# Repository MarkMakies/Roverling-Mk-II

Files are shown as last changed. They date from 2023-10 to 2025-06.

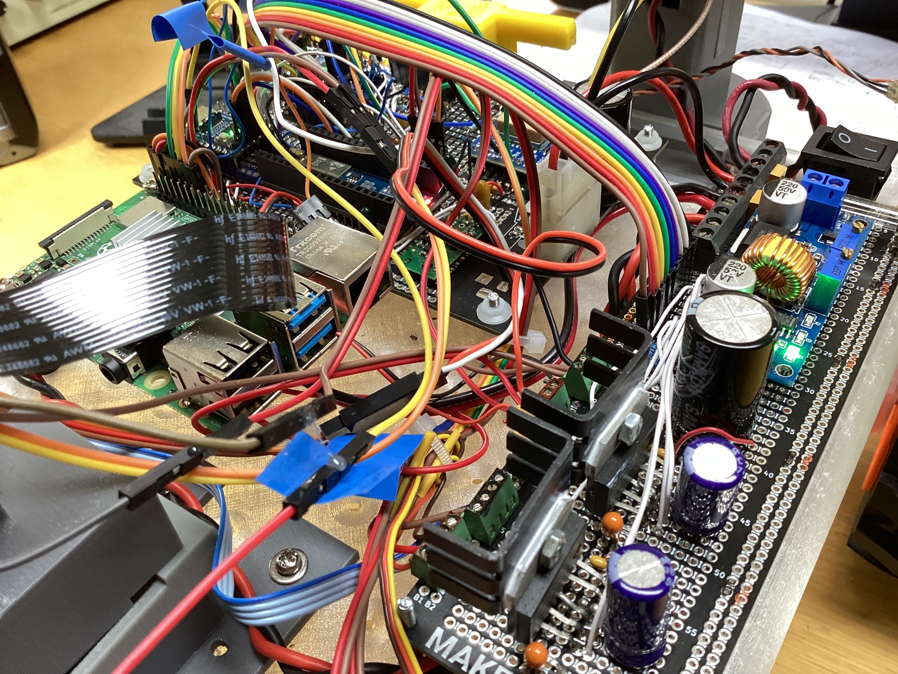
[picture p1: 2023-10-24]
Electronics/IMG_1050.JPEG

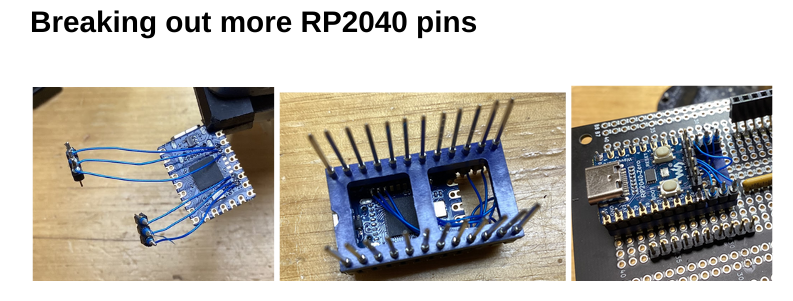
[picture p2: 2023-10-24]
Electronics/Screenshot_2023-10-25_10-17-56.png

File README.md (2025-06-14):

## Roverling Mk II
# A cheap multipurpose mobile robotic platform for research, development, education and fun
All design files, schematics & code available in this repository.  

Build tutorial [here](https://makies.com.au/roverlingmkii/).

**2025 Update:** Started working on an updated version to support my autonomous metal detector project.  Documenting progress on Hackaday.io.  

---

### STAGE 1 - Mecha Design July 2023

cad

### STAGE 1 - Complete Aug 2023

rv2a

### Stage 2 - Tronics design wish list Sep 2023

rv2b

### Stage 2 - MPU code development and electronics complete Oct 2023



### Stage 3 - GUI complete as well as LoRa /WiFi /MQTT gateway.  



## And now, Oct 2023,  writing it all up so others can understand and follow I hope :) 

in progress.....

# Why did I start this project:   

A few months back I created a basic mobile platform using parts from an old 3D printer.  It was fun but not very practical.

I designed Roverling Mark II so I could experiment with a practical, configurable and reliable  mobile platform.  Hopefully one day getting it to do some useful stuff around our bush block, like

      - Searching paddocks for weeds and recording locations.
      - Navigating down a 200m drive to check if the gate is closed.
      - Navigating up the drive 50m to check that the machine shed roller doors are secure.
      - Recording animal sightings on the block.  We’d see up to 50 roos per day on our block.
      - It would be good to identify and scare deer away from our olive grove.
      - And a friend already wants to mount a metal detector and do automatic scanning of a large area.

Anyway, to that end, here is the complete design and everything you need to know to make your own or any variation.  As much as possible I’ve kept the cost down to a minimum, reused some older parts and printed as much as possible.

This is a current work in progress.  At some stage I needed to draw the line and write something up before it gets too big.  So these are the current working and operational specifications

     - 440 mm long x 350 mm wide, 250 mm max height, 200 mm nominal platform height
     - 3.5 kg without battery, uses an 18V power tool battery
     - Up to 22 satellite GNSS receiver, augmentation using SBAS, 1Hz updates
     - IMU: 3x accel, 3x gyro, magnetometer, pressure
     - 2.4Ghz 6 channel RC receiver and decoder, with diverse receiver
     - 2 channel motor quadrature decoders 
     - 2 channel motor current sensors (effectively torque sensors)
     - Sonar, ranger
     - 915 Mhz LoRa module.  Comms at 1800 bps,  64 byte telemetry packet, 16 byte command packet, encrypted, super reliable
      LoRa base station, which is effectively my MQTT gateway for telemetry and commands back
     - Mapping module runs on desktop from MQTT feed to produce realtime tracking info overlaid on an image (for me an old NearMap screenshot).
      On board RPi 4B w/ 4G running the latest OS with a camera 3 module.  

All the 3D design is done in FreeCAD and all the slicing and printing on a Prusa platform.  As well as the actual design files, I’ve also made available stl model files, g-code files and Prusa project files for all parts.

The schematic is done with KiCAD.  I used mixed prototyping methods and no PCB has been designed (yet) so you will need a fair understanding of how to layout and wire correctly.

All the code is in python.  I’ve pretty much written my own drivers for all of the low level stuff except the sx1262 suite for LoRa and MQTT.  I’ve tried to document as much as possible.

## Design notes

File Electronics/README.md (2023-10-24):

## KiCAD schematic diagram in R202 directory.

PCB not yet designed.

First prototype pics give an idea of how to wire.

## Major Parts List

- 1x 	Adafruit Ultimate GPS Breakout with GLONASS + GPS - PA1616D - 99ch 10 Hz
- 1x 	SMA to uFL/u.FL/IPX/IPEX RF Adapter Cable
- 1x 	Makerverse Project Proto - Protoboard with Power Breakouts
- 6x	2.54mm Pitch 4-Pin Screw Terminal Block
- 2x	RP2040-Zero, a Pico-like MCU Board Based on Raspberry Pi RP2040
- 1x	Raspberry Pi Pico W (for LoRa / MQTT gateway)
- 1x	GPS/GNSS Magnetic Mount Antenna SMA - 3m
- 1x	AltIMU-10 v6 Gyro, Accelerometer, Compass, and Altimeter 
- 2x	SX1262 LoRa Node Module for Raspberry Pi Pico, LoRaWAN
- 1x	915MHz LoRa Antenna RP-SMA - 1/4 Wave 2dBi
- 1x	PIR Infrared Motion Sensor (HC-SR501)
- 1x	XL-MaxSonar-EZ0 Sonar Range Finder MB1200
- 1x	DC-DC Adjustable Step-down Module 5A 75W
- 2x	LMD18200, 3A, 55V H-Bridge, or similar

For later projects and video capture only at this stage
- 1x	Raspberry Pi 4 Model B 4GB 
- 1x	Raspberry Pi Camera Module 3

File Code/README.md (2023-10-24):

Which code goes into which MPU...

## Motion Processor
###### (MicroPython v1.20.0 on 2023-04-26; Raspberry Pi Pico with RP2040)

Works independently of other modules.  Can use RC to control without any other modules.
On RC toggle FLAPS to put into RC mode.  Onboard LED will change from steady green to flashing pink.
Ensure throttle is at min first.  Ailerons control steering, elevator controls camera tilt.  GEAR
puts it into reverse mode.

	MPU/mainM.py 			rename to main.py
	MPU/Comms.py                 	inter-MPU Comms
	MPU/QuadDec.py			Motor quadrature decoder (PIO/SM based)
	MPU/RCinterface.py  		6 channel RC interface (interrupt based)

## Telemetry Processor 
###### (MicroPython v1.20.0 on 2023-04-26; Raspberry Pi Pico with RP2040)

Aggregates ALL data from platform for telemetery transmission over LoRa at around 1800bps.  Accepts
LoRa commands. Telemetry includes:

	GPS: 		quality, number satellites, accuracy, altitude, lat & long with 7 decimal places precision
	IMU: 		acceleration (X,Y,Z), gyroscope (X, Y, Z), magnetometer (X, Y, Z), temperature, pressure
	Locomotion: 	velocity (L/R), torque/current (L/R), power delivered (L/R)
	RC: 		6 channels, 0 to 100%
	Platform: 	PIR, sonar range, battery level, status bits
	Comms:  	RSSI & SNR for both Roverling and Base Station ends

&nbsp;
 
	MPU/mainT.py 			rename to main.py
	MPU/GPS.py			Configure and then read GPS module data
	MPU/IMU.py			Intertial measurement unit interface
	MPU/Comms.py			inter-MPU Comms
	MPU/Packets.py			telemetry and control LoRa packet assembly and disassembly
	MPU/Secrets.py			modify and rename Secret_Example.py to Secrets.py
		
	MPU/lib/_sx126x.py 		LoRa drivers from https://github.com/ehong-tl/micropySX126X/tree/master
	MPU/lib/sx1262.py		LoRa drivers from https://github.com/ehong-tl/micropySX126X/tree/master
	MPU/lib/sx126x.py 		LoRa drivers from https://github.com/ehong-tl/micropySX126X/tree/master

## Telemetry Gateway Processor  
###### (MicroPython v1.20.0 on 2023-04-26; Raspberry Pi Pico W with RP2040)

Provides a gateway for Roverling LoRa commands and telemetry to MQTT message broker over WiFi.  Onboard LED
flashes blue when commands are received.  A sigle message is delivered twice a second, and looks a lot like this. (On MQTT Explorer): 
(3172, '-37.0000000, 144.0000000', 1, 4, 3.0, 640.4, 0.0, 0.0, 0.039, 0.043, 0, 0, 10, 50, 51, 51, 9, 10, 0.013, -0.037, 1.015, 0, 0, 0, 0.034, -0.037, 0.455, 19.734, 944.5, 10.25, -42.0, 384, 0, 0, 0, 11.0, -45.0)
	
	MPU/mainG.py 			rename to main.py
	MPU/Packets.py			telemetry and control LoRa packet assembly and disassembly
	MPU/Secrets.py			modify and rename Secret_Example.py to Secrets.py
	
	MPU/lib/_sx126x.py 		LoRa drivers from https://github.com/ehong-tl/micropySX126X/tree/master
	MPU/lib/sx1262.py		LoRa drivers from https://github.com/ehong-tl/micropySX126X/tree/master
	MPU/lib/sx126x.py 		LoRa drivers from https://github.com/ehong-tl/micropySX126X/tree/master
	
	MPU/lib/umqttsimple.py		MQTT module from https://pypi.org/project/micropython-umqtt.simple/#files

## Block Diagram 


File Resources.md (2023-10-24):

### Roverling References

    https://core-electronics.com.au/raspberry-pi-camera-3.html
    https://www.lloydbrombach.com/post/calibrating-a-magnetometer-for-accurate-compass-headings
    https://cdn-shop.adafruit.com/datasheets/GlobalTop-FGPMMOPA6H-Datasheet-V0A.pdf
    https://core-electronics.com.au/raspberry-pi-4-model-b-4gb.html
    https://core-electronics.com.au/dc-dc-adjustable-step-down-module-5a-75w.html
    https://maxbotix.com/pages/xl-maxsonar-ez-datasheet
    https://core-electronics.com.au/modmypi-pir-infrared-motion-sensor-hc-sr501.html
    https://core-electronics.com.au/attachments/localcontent/lps22df_14783eca5bc.pdf
    https://core-electronics.com.au/attachments/localcontent/LIS3MDL_1697332cae7.pdf
    https://core-electronics.com.au/attachments/localcontent/lsm6dso_2893604b03c.pdf
    https://core-electronics.com.au/altimu-10-v6-gyro-accelerometer-compass-and-altimeter-lsm6dso-lis3mdl-and-lps22df-carrier.html
    https://aprs.gids.nl/nmea/
    https://cdn-shop.adafruit.com/datasheets/PMTK_A08.pdf
    https://core-electronics.com.au/adafruit-ultimate-gps-breakout-66-channel-w-10-hz-updates-version-3.html
    https://www.waveshare.com/w/upload/e/e1/DS_SX1261-2_V1.2.pdf
    https://core-electronics.com.au/sx1262-lora-node-module-for-raspberry-pi-pico-lorawan.html
    https://www.maxongroup.com/medias/sys_master/root/8883971129374/EN-21-483.pdf
    https://www.ti.com/lit/ds/symlink/lmd18200.pdf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
    http://www.ee.nmt.edu/~wedeward/EE382/SP01/2332_11W_motor.pdf
    https://core-electronics.com.au/raspberry-pi-pico-w-wireless-wifi.html
    https://docs.google.com/document/d/1ch-O_GQVIoLGmJAj2cPDHbGdn4rwzycuPbIQoS8rBxI/edit
    https://core-electronics.com.au/rp2040-zero-a-pico-like-mcu-board-based-on-raspberry-pi-mcu-rp2040-mini-ver-1.html

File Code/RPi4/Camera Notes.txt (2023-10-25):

24/10/2023
CAPTURE
libcamera-vid --codec h264 --nopreview --inline --width 1280 --height 720 --rotation 180  --framerate 30 -t 0 -o test.h264
ffplay test.h264

CONVERT
ffmpeg -framerate 15 -i test2cam.h264 -c copy test2cam.mp4

STREAM TCP
libcamera-vid --codec h264 --nopreview --inline --width 1920 --height 1080 --rotation 180  --framerate 30 --listen -t 0 -o tcp://0.0.0.0:10001
ffplay tcp://192.168.2.20:10001 -fflags nobuffer -flags low_delay -framedrop

STREAM UDP
libcamera-vid --codec h264 --nopreview --inline --width 1920 --height 1080 --rotation 180  --framerate 30 -t 0 -o udp://192.168.2.1:10001
ffplay udp://:10001 -fflags nobuffer -flags low_delay -framedrop

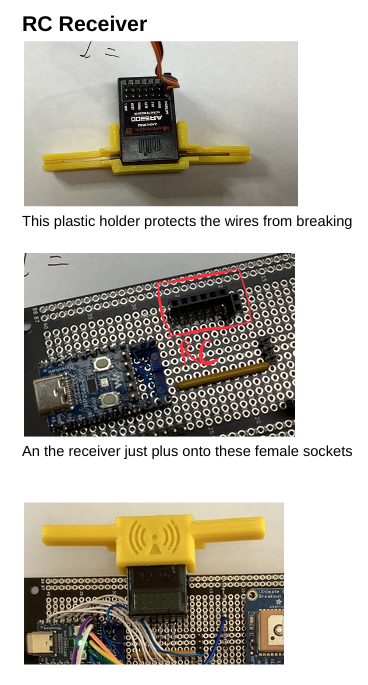
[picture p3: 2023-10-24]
Electronics/Screenshot_2023-10-25_10-19-28.png

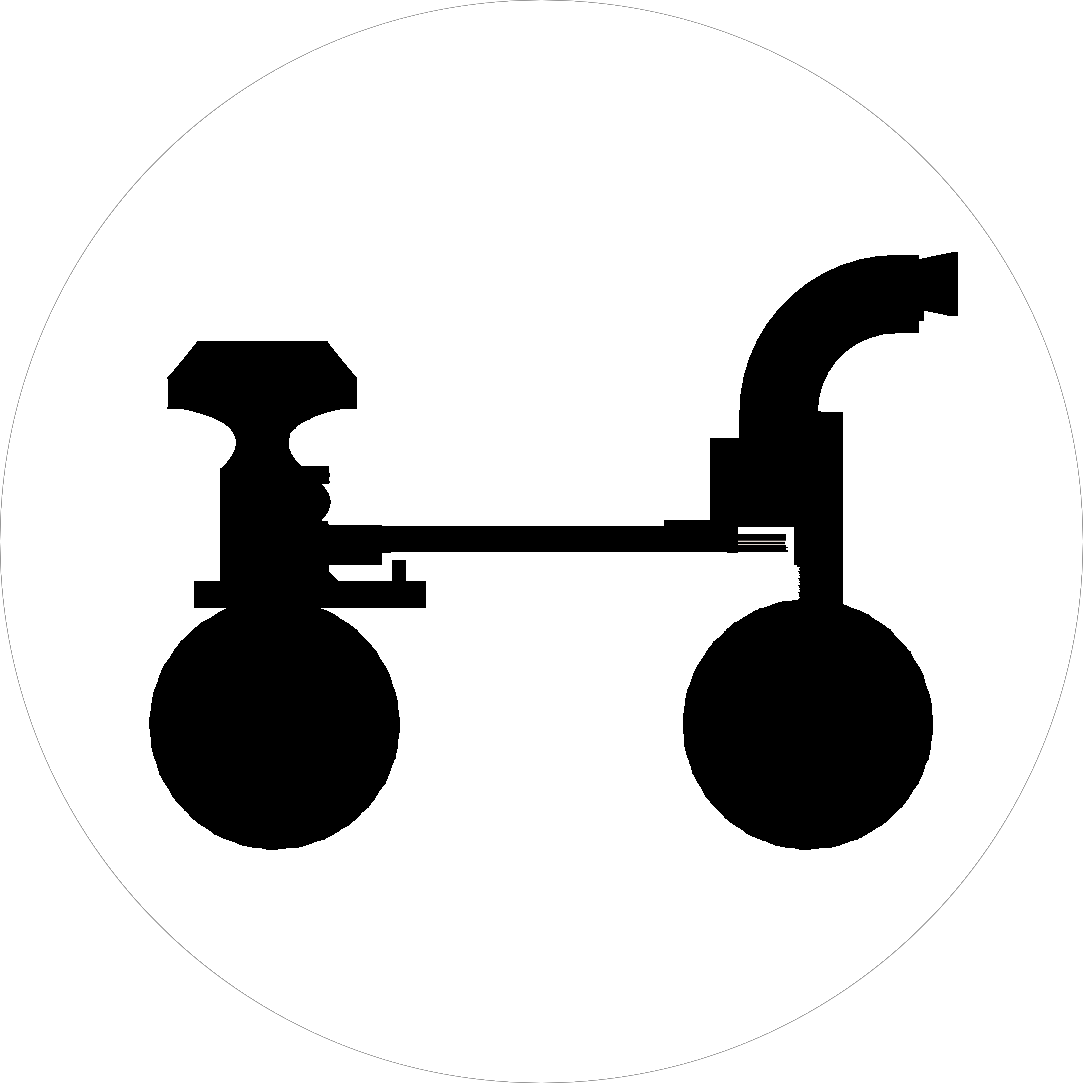
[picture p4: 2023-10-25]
Code/Desktop/RovSide3.png

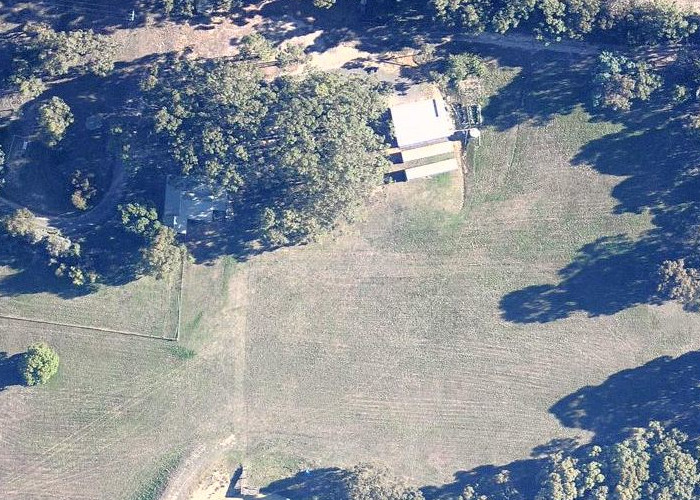
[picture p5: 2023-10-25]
Code/Desktop/map1.JPG

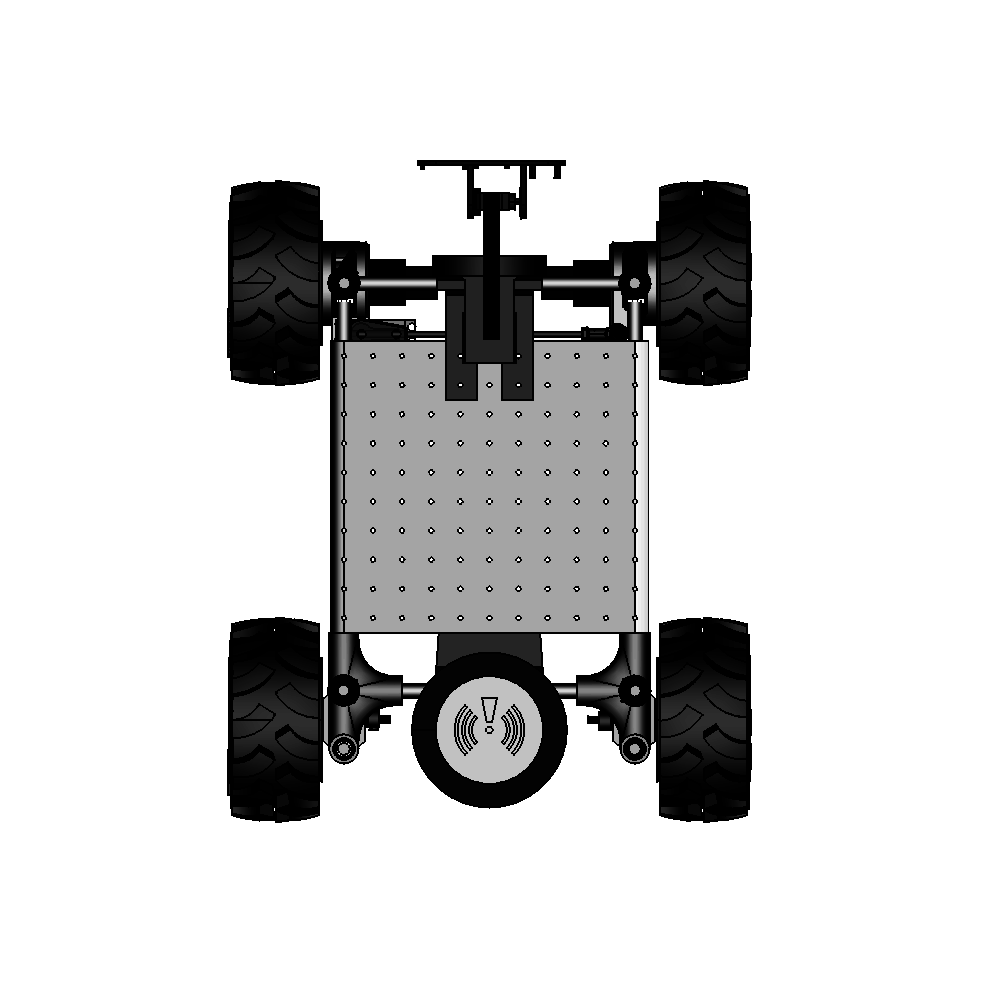
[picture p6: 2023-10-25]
Code/Desktop/RovTop6.png

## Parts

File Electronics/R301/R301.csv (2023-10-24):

Source: | /home/mark/Things/CAD/Roverling102/Roverling102.kicad_sch
Date: | Thu 20 Jul 2023 12:56:17
Tool: | Eeschema 6.0.2+dfsg-1
Generator: | /usr/share/kicad/plugins/bom_csv_grouped_by_value.py
Component Count: | 47
Individual Components:
Item | Qty | Reference(s) | Value | LibPart | Footprint | Datasheet
 |  | C1 | 100n | Device:C_Small |  | ~
 |  | C2 | 100n | Device:C_Small |  | ~
 |  | C3 | 470u | Device:C_Polarized |  | ~
 |  | C4 | 470uF | Device:C_Polarized |  | ~
 |  | C5 | 100n | Device:C_Small |  | ~
 |  | C6 | 100n | Device:C_Small |  | ~
 |  | C7 | 100n | Device:C_Small |  | ~
 |  | C8 | 470u | Device:C_Polarized |  | ~
 |  | C9 | 100n | Device:C_Small |  | ~
 |  | C10 | 100n | Device:C_Small |  | ~
 |  | C11 | 100n | Device:C_Small |  | ~
 |  | C12 | 470uF | Device:C_Polarized |  | ~
 |  | C13 | 47u | Device:C_Polarized |  | ~
 |  | C14 | 100n | Device:C_Small |  | ~
 |  | C15 | 47u | Device:C_Polarized |  | ~
 |  | F1 | 10A | Device:Fuse |  | ~
 |  | J1 | Screw_Terminal | Connector:Screw_Terminal_01x10 |  | ~
 |  | J2 | Screw_Terminal | Connector:Screw_Terminal_01x10 |  | ~
 |  | J3 | Screw_Terminal_01x02 | Connector:Screw_Terminal_01x02 |  | ~
 |  | J4 | Conn_01x03 | Connector_Generic:Conn_01x03 |  | ~
 |  | J6 | Conn_01x03 | Connector_Generic:Conn_01x03 |  | ~
 |  | J7 | Conn_01x03 | Connector_Generic:Conn_01x03 |  | ~
 |  | J8 | Conn_01x03 | Connector_Generic:Conn_01x03 |  | ~
 |  | J9 | Conn_01x03 | Connector_Generic:Conn_01x03 |  | ~
 |  | J10 | Conn_01x03 | Connector_Generic:Conn_01x03 |  | ~
 |  | M1 | 17HDC1031-20B | Motor:Stepper_Motor_bipolar |  | http://www.infineon.com/dgdl/Application-Note-TLE8110EE_driving_UniPolarStepperMotor_V1.1.pdf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
 |  | R1 | 4k7 | Device:R_US |  | ~
 |  | R2 | 10k | Device:R_US |  | ~
 |  | R4 | 4k7 | Device:R_US |  | ~
 |  | R5 | 4k7 | Device:R_US |  | ~
 |  | R7 | 10k | Device:R_US |  | ~
 |  | R8 | 10k | Device:R_US |  | ~
 |  | R9 | 4k7 | Device:R_US |  | ~
 |  | R10 | 4k7 | Device:R_US |  | ~
 |  | R11 | 4k7 | Device:R_US |  | ~
 |  | R12 | 10k | Device:R_US |  | ~
 |  | R13 | 10k | Device:R_US |  | ~
 |  | R14 | 10k | Device:R_US |  | ~
 |  | R15 | 160k | Device:R_US |  | ~
 |  | SW1 | SW_SPST_LED | Switch:SW_SPST_LED |  | ~
 |  | U1 | RP2040-Zero | _MM:RP2040-Zero | RP2040-Zero:RP2040-Zero
 |  | U2 | A4988 | :Pololu_Breakout_A4988_1 | Module:Pololu_Breakout-16_15.2x20.3mm | https://www.pololu.com/product/2980/pictures
 |  | U3 | A4988 | :Pololu_Breakout_A4988_2 | Module:Pololu_Breakout-16_15.2x20.3mm | https://www.pololu.com/product/2980/pictures
 |  | U4 | A4988 | :Pololu_Breakout_A4988_3 | Module:Pololu_Breakout-16_15.2x20.3mm | https://www.pololu.com/product/2980/pictures
 |  | U5 | A4988 | Driver_Motor:Pololu_Breakout_A4988 | Module:Pololu_Breakout-16_15.2x20.3mm | https://www.pololu.com/product/2980/pictures
 |  | U6 | DFR0568 (2.5~15V to 3.3V 600mA) | Regulator_Switching:CRE1S0505DC | Converter_DCDC:Converter_DCDC_Murata_CRE1xxxxxxDC_THT | http://power.murata.com/datasheet?/data/power/ncl/kdc_cre1.pdf
 |  | U7 | DFR0569 (3~15V to 5V 600mA) | Regulator_Switching:CRE1S0505DC | Converter_DCDC:Converter_DCDC_Murata_CRE1xxxxxxDC_THT | http://power.murata.com/datasheet?/data/power/ncl/kdc_cre1.pdf
Collated Components:
Item | Qty | Reference(s) | Value | LibPart | Footprint | Datasheet
1 | 9 | C1, C2, C5, C6, C7, C9, C10, C11, C14 | 100n | Device:C_Small |  | ~
2 | 2 | C3, C8 | 470u | Device:C_Polarized |  | ~
3 | 2 | C4, C12 | 470uF | Device:C_Polarized |  | ~
4 | 2 | C13, C15 | 47u | Device:C_Polarized |  | ~
5 | 1 | F1 | 10A | Device:Fuse |  | ~
6 | 2 | J1, J2 | Screw_Terminal | Connector:Screw_Terminal_01x10 |  | ~
7 | 1 | J3 | Screw_Terminal_01x02 | Connector:Screw_Terminal_01x02 |  | ~
8 | 6 | J4, J6, J7, J8, J9, J10 | Conn_01x03 | Connector_Generic:Conn_01x03 |  | ~
9 | 1 | M1 | 17HDC1031-20B | Motor:Stepper_Motor_bipolar |  | http://www.infineon.com/dgdl/Application-Note-TLE8110EE_driving_UniPolarStepperMotor_V1.1.pdf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
10 | 6 | R1, R4, R5, R9, R10, R11 | 4k7 | Device:R_US |  | ~
11 | 6 | R2, R7, R8, R12, R13, R14 | 10k | Device:R_US |  | ~
12 | 1 | R15 | 160k | Device:R_US |  | ~
13 | 1 | SW1 | SW_SPST_LED | Switch:SW_SPST_LED |  | ~
14 | 1 | U1 | RP2040-Zero | _MM:RP2040-Zero | RP2040-Zero:RP2040-Zero
15 | 1 | U2 | A4988 | :Pololu_Breakout_A4988_1 | Module:Pololu_Breakout-16_15.2x20.3mm | https://www.pololu.com/product/2980/pictures
16 | 1 | U3 | A4988 | :Pololu_Breakout_A4988_2 | Module:Pololu_Breakout-16_15.2x20.3mm | https://www.pololu.com/product/2980/pictures
17 | 1 | U4 | A4988 | :Pololu_Breakout_A4988_3 | Module:Pololu_Breakout-16_15.2x20.3mm | https://www.pololu.com/product/2980/pictures
18 | 1 | U5 | A4988 | Driver_Motor:Pololu_Breakout_A4988 | Module:Pololu_Breakout-16_15.2x20.3mm | https://www.pololu.com/product/2980/pictures
19 | 1 | U6 | DFR0568 (2.5~15V to 3.3V 600mA) | Regulator_Switching:CRE1S0505DC | Converter_DCDC:Converter_DCDC_Murata_CRE1xxxxxxDC_THT | http://power.murata.com/datasheet?/data/power/ncl/kdc_cre1.pdf
20 | 1 | U7 | DFR0569 (3~15V to 5V 600mA) | Regulator_Switching:CRE1S0505DC | Converter_DCDC:Converter_DCDC_Murata_CRE1xxxxxxDC_THT | http://power.murata.com/datasheet?/data/power/ncl/kdc_cre1.pdf

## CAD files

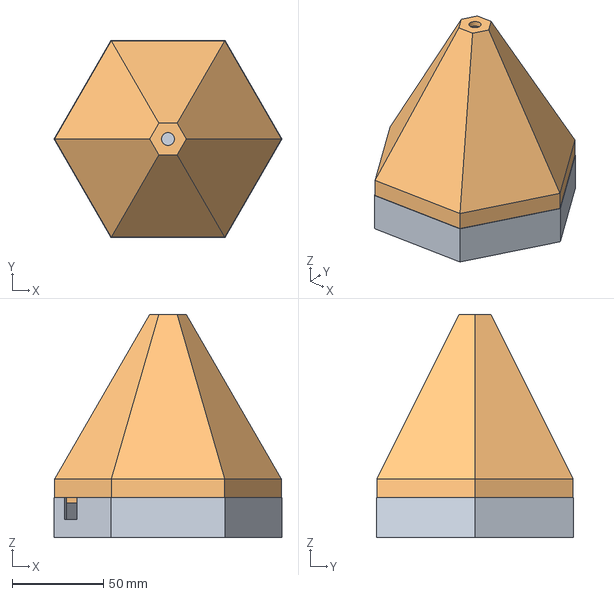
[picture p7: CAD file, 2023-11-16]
3D/LoRaGateWay101.FCStd
124.6 x 107.9 x 122.0 mm
Base
Top

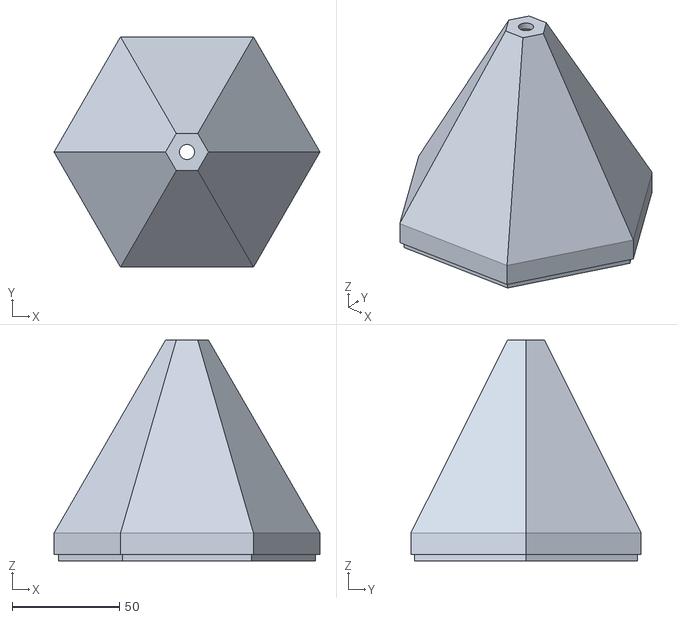
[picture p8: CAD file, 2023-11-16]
3D/Model/LoRaGateWay101-Top.stl
124.0 x 107.4 x 103.0

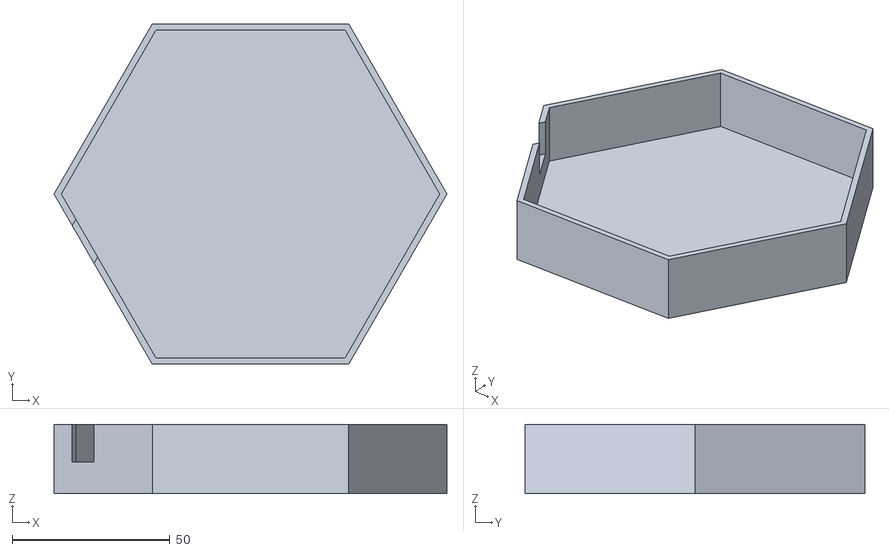
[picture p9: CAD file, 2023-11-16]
3D/Model/LoRaGateWay101-Base.stl
124.6 x 107.9 x 22.0

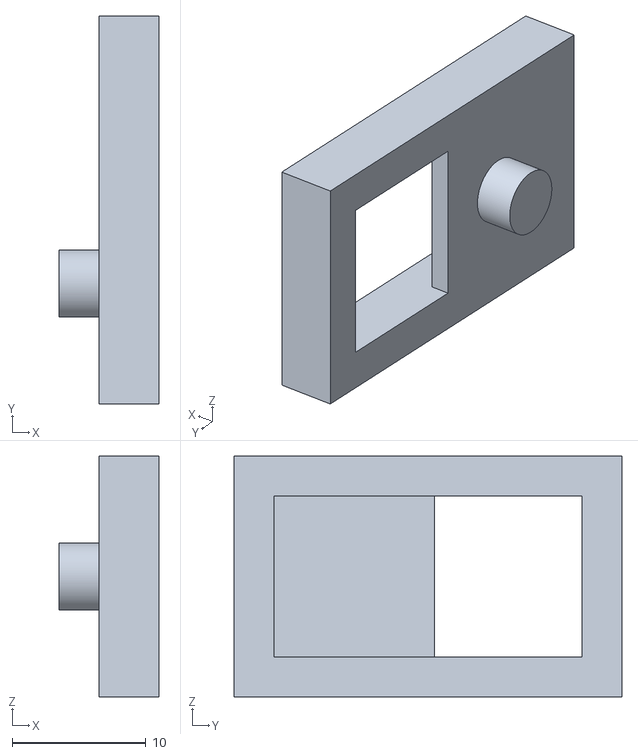
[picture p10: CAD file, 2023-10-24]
3D/Model/R208-Servo-Bearing-Holder.stl
7.50 x 29.0 x 18.0

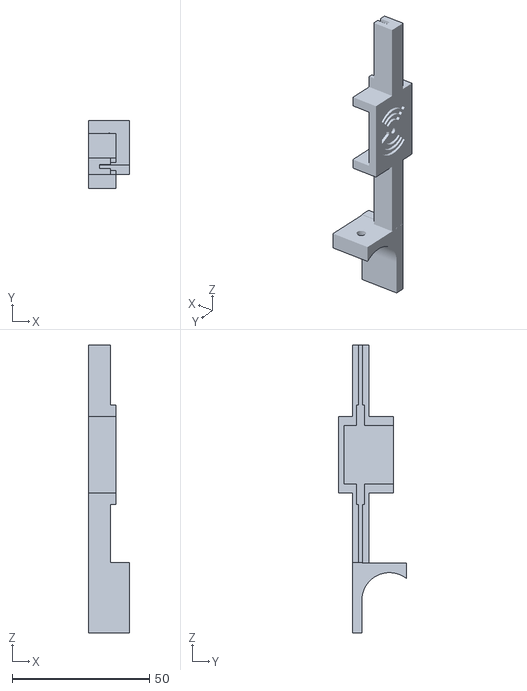
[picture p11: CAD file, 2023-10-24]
3D/Model/R207-RC-Sat-Ant.stl
15.0 x 24.7 x 105.0

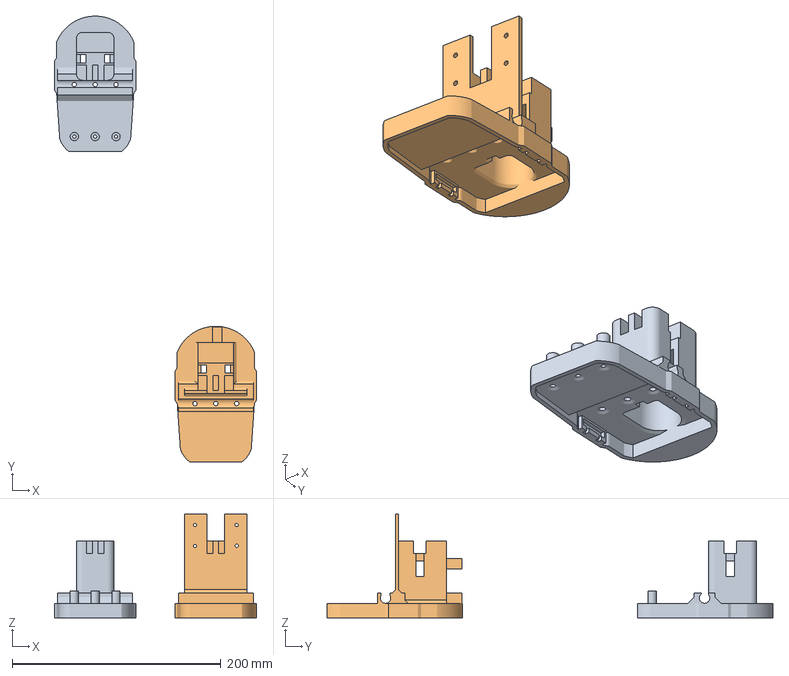
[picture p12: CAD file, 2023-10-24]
3D/Prusa/R208-Battery-Carrier-Front-R1.3mf
193.6 x 427.3 x 99.5 mm
R205-Battery Carrier.stl
R208-Battery-Carrier-Front.stl

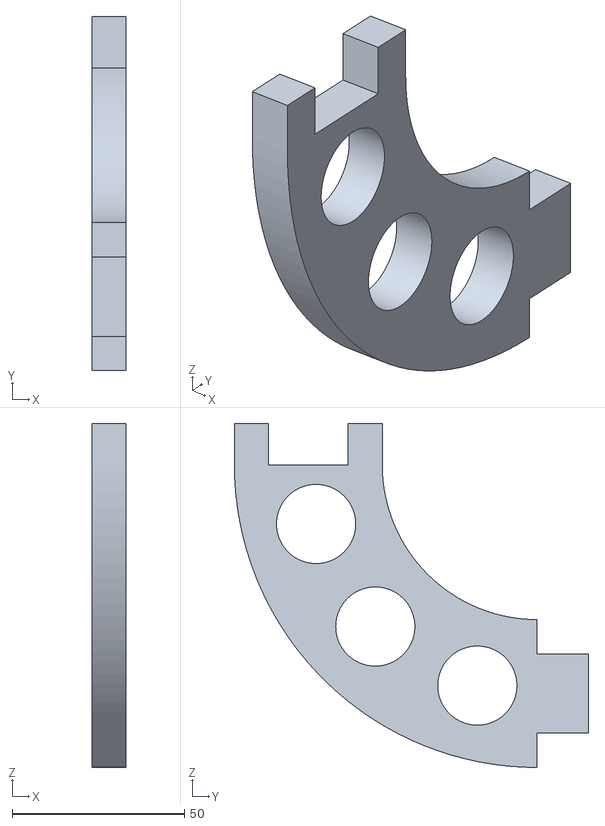
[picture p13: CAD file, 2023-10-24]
3D/Model/R208-Cam-Servo-Mount.stl
10.0 x 103.0 x 100.0

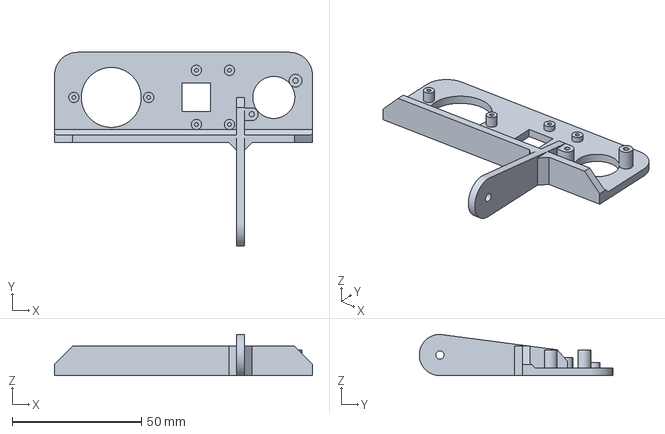
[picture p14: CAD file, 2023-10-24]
3D/Prusa/R208-Sensor-Array.3mf
100.0 x 75.0 x 16.0 mm

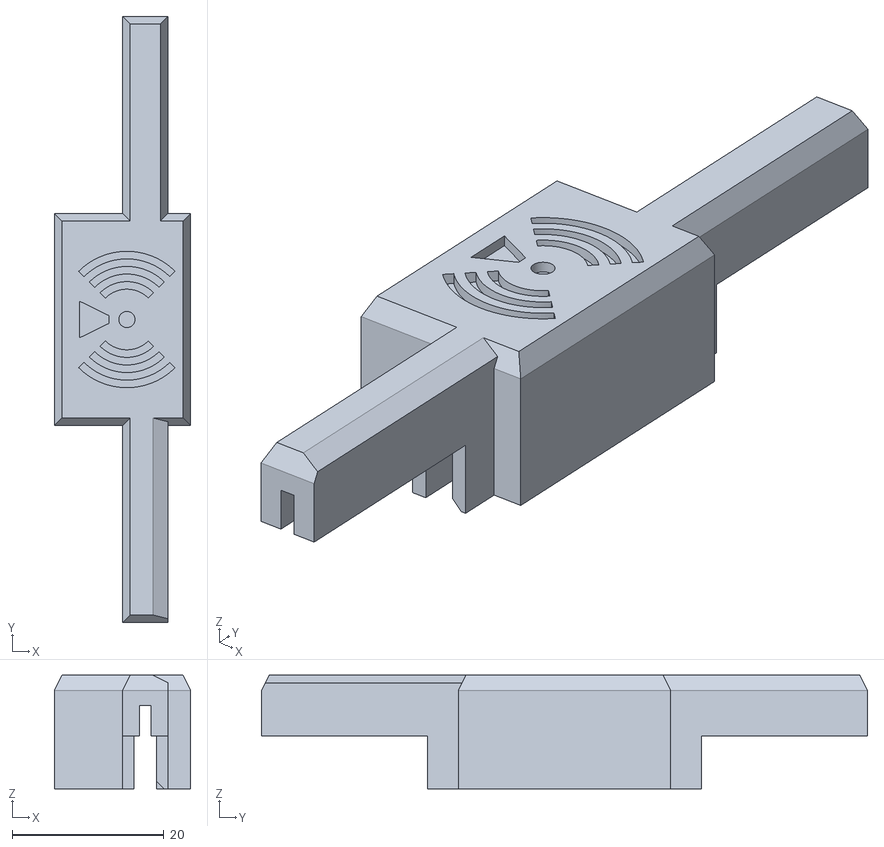
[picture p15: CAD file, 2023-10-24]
3D/Model/R207-RC Ant.stl
18.0 x 80.0 x 15.0

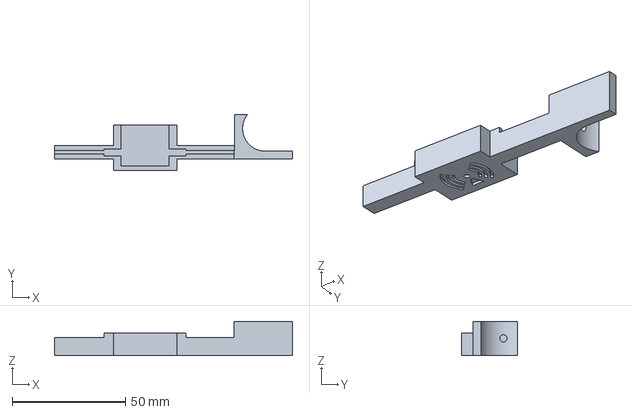
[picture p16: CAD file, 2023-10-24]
3D/Prusa/R207-RC-Sat-Ant-R1.3mf
105.0 x 24.7 x 15.0 mm

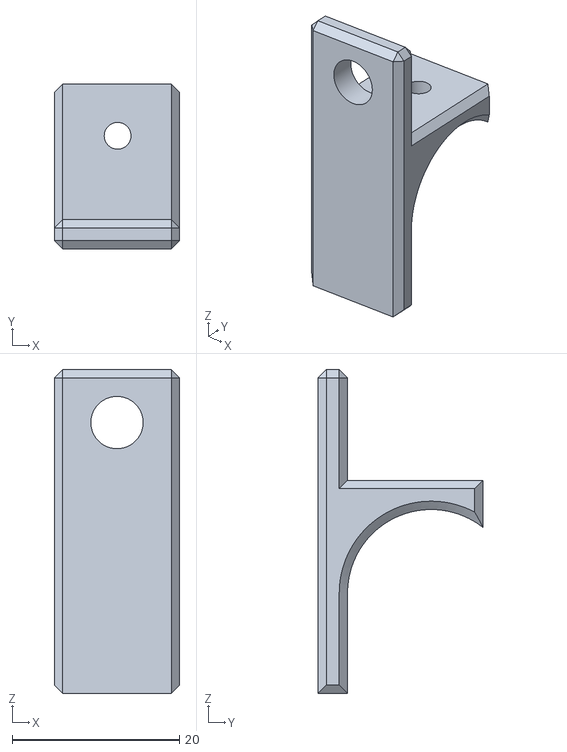
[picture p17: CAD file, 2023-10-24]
3D/Model/R207-Antenna-Bracket.stl
15.0 x 19.7 x 38.8

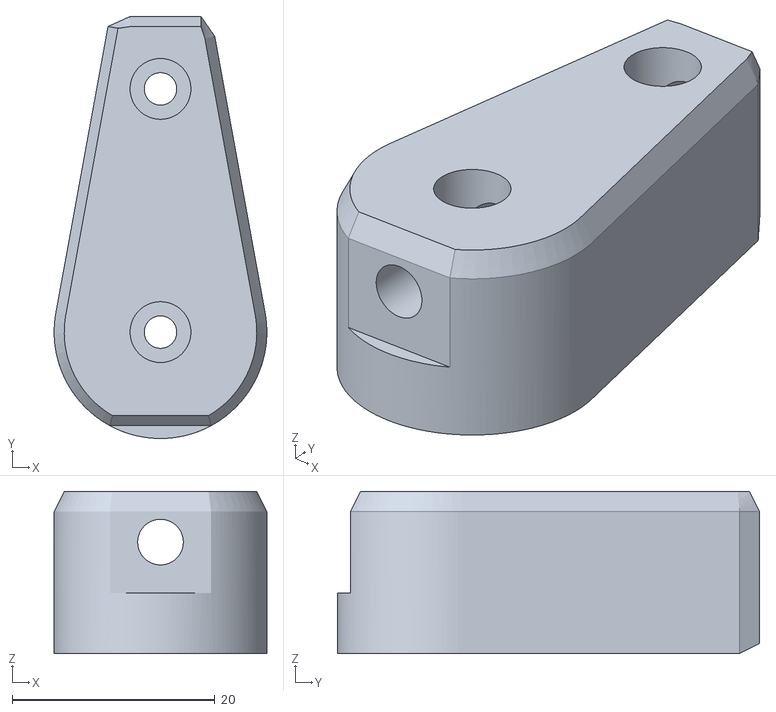
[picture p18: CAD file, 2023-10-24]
3D/Model/R208-Servo-Horn.stl
21.0 x 41.6 x 16.0

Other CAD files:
3D/Prusa/LoRaGateWay101-Top-R1.3mf
3D/Prusa/LoRaGateWay101-Base-R1.3mf
3D/Prusa/R208-Servo-Bearing-Holder-R1.3mf
3D/Model/R208-Sensor-Array.stl
3D/Prusa/R207-RC Ant-R1.3mf
3D/Prusa/R207-Antenna-Bracket-R1.3mf
3D/Model/R205-Antenna-Base.stl
3D/Model/R205-Antenna-Cover.stl
3D/Model/R205-Battery Carrier.stl
3D/Model/R205-Corner-Front-x2.stl
3D/Model/R205-Hub Front Right-x1.stl
3D/Model/R205-Hub-Front-Left-x1.stl
3D/Model/R205-Hub-Rear-x2.stl
3D/Model/R205-Platform.stl
3D/Model/R205-Tyre-Label.stl
3D/Model/R205-Tyre-x2-m2.stl
3D/Model/R205-Wheel-Front-x2.stl
3D/Model/R205-Wheel-Rear-x2.stl
3D/Model/R206-Corner-Back-Right-x1.stl
3D/Model/R206-Flex-Stop-x4.stl
3D/Model/R206-Hub-Rear-x2.stl
3D/Model/R208-Adapter-Mod.stl
3D/Model/R208-Battery-Carrier-Front.stl
3D/Model/R208-Sensor-Bar.stl
3D/Prusa/R205-Antenna-Base-R1.3mf
3D/Prusa/R205-Antenna-Cover-R1.3mf
3D/Prusa/R205-Battery-Carrier-R1.3mf
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

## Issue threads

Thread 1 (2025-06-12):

Loving this project - chance of a simpler version?

KodeMunkie, 2025-06-12:
I'm unlikely to be able to find the time to build this (I really want to!), is there a possibility of a MK3 "lite" version that has lora, GPS, camera and not much else?

My ultimate dream is to build an automated wheelchair/seated quad which could take verbal instructions, and although I have some experience with electronics (and a lot of programming) the current design, regrettably, as a testing / feasibility platform is too complex for me to prototype quickly.

A tutorial say with 4 stages would be manageable e.g. frame, sensors, motion, brain.

MarkMakies, 2025-06-12:
Thanks for your message and your interest in Roverling!

At the moment, I’m tied up with a number of other projects, including a Roverling upgrade I’m documenting on [Hackaday](https://hackaday.io/project/203299-roverling-mk-ii), but it’s actually heading in the opposite direction to what you’re after. I’ve removed the Raspberry Pi, camera, and sonar, and I’m now focusing on improving navigation accuracy, autonomy, and terrain handling.

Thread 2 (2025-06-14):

Link in the readme fails

vortex314, 2025-06-14:
The link to code and drawings fails, 404

MarkMakies, 2025-06-14:
Code, drawings, schematics, 3D, etc all here.

The original tutorial was hosted by Core Electronics but it had been deleted.  Link changed and now points to new tutorial [location](https://makies.com.au/roverlingmkii/).

Closed 2025-06-14.

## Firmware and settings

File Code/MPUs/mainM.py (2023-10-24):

################################################################################
# Roverling Mk II - Motor Control Processor
print('Roverling Mk II - Motor & RC Control main.py on RP2040')

from machine import Pin, PWM, ADC, UART
from time import sleep_ms
from gc import collect
import neopixel

# my modules
from RCinterface import dataR
from QuadDec import dataV
from Comms import SendTelemetry, RecvCommand, dataCMD

Muart = UART(1, baudrate=1_000_000, tx=Pin(8), rx=Pin(9))

################################################################################
# LED

NeoPin = Pin(16,Pin.OUT)
Neo = neopixel.NeoPixel(NeoPin,1)
LastLEDstate = True
RGBon, RGBoff = (20,0,0), (0,0,0)

Neo[0]=(20, 0, 0)
neopixel.NeoPixel.write(Neo)

def LEDupdate(mode='none'):
    global Neo, LastLEDstate, RGBon, RGBoff

    if mode == 'GreenSolid':
        RGBon, RGBoff = (20,0,0), (20,0,0)
    elif mode == 'RedSolid':
        RGBon, RGBoff = (0,20,0), (0,20,0)
    elif mode == 'YellowFlash':
        RGBon, RGBoff = (6,20,0), (0,0,0)
    elif mode == 'PinkFlash':
        RGBon, RGBoff = (5,50,10), (0,0,0)

    if not LastLEDstate:
        Neo[0] = RGBon
        LastLEDstate = True
    else:
        Neo[0] = RGBoff
        LastLEDstate = False

    neopixel.NeoPixel.write(Neo)

LEDupdate('RedSolid')

################################################################################
# Motor Current
Lsens = ADC(Pin(28))
Rsens = ADC(Pin(29))

def GetMotorI():       
    global LMamps, RMamps
    ICoeff = 20000  # 377uA/A, over 2k2, => 0.894 V/A
    LMamps = Lsens.read_u16() / ICoeff
    RMamps = Rsens.read_u16() / ICoeff

################################################################################
# Motor Control LM18200 H-bridge

PWMfreq = 50000

LeftDIR = Pin(15, Pin.OUT, value = 0)
LeftBRK = Pin(25, Pin.OUT, value = 1)
LeftPWM = PWM(Pin(27))
LeftPWM.freq(PWMfreq)
LeftPWM.duty_u16(0)

RightDIR = Pin(14, Pin.OUT, value = 0)
RightBRK = Pin(24, Pin.OUT, value = 1)
RightPWM = PWM(Pin(26))
RightPWM.freq(PWMfreq)
RightPWM.duty_u16(0)

def MotDrive(left = 'off', right = 'off'):
    global LeftPower, RightPower
    maxPWM = 2**16 - 1
    if left == 'off':           # driver off, no current
        LeftPWM.duty_u16(0)
        LeftBRK.value(1)
        LeftPower = 0
    else:
        LD = int(left)
        if LD == 0:             # active brake: source 1 & source 2
            LeftPWM.duty_u16(maxPWM)
            LeftBRK.value(1)
            LeftDIR.value(0)
            LeftPower = 0
        elif LD > 0:            # going forward:" source 1 & sink 2"
            LeftPWM.duty_u16(LD)
            LeftBRK.value(0)
            LeftDIR.value(1)
            LeftPower = LD
        else:                   # going back:" sink 1 & source 2"
            LeftPWM.duty_u16(0-LD)
            LeftBRK.value(0)
            LeftDIR.value(0)   
            LeftPower = LD         
    
    if right == 'off':  
        RightPWM.duty_u16(0)
        RightBRK.value(1)
        RightPower = 0
    else:
        RD = int(right)
        if RD == 0:  
            RightBrake = True
            RightPWM.duty_u16(maxPWM)
            RightBRK.value(1)
            RightDIR.value(0)
            RightPower = 0
        elif RD > 0:            
            RightPWM.duty_u16(RD)
            RightBRK.value(0)
            RightDIR.value(0)
            RightPower = RD
        else:
            RightPWM.duty_u16(0-RD)
            RightBRK.value(0)
            RightDIR.value(1)  
            RightPower = RD   

MotDrive()

################################################################################
# Steering Servo
# 20ms cycle, pulse 1-2ms, range adj - trial and error to find limits

Scentre = 5300
Slow = 3900         # +/- 30 deg
Shigh = 6200

SteeringServo = PWM(Pin(18))
SteeringServo.freq(50)
SteeringServo.duty_u16(Scentre)

PanServo = PWM(Pin(6))
PanServo.freq(50)

Tlow  = 3300
Tcentre = 4900
Thigh = 8000

TiltServo = PWM(Pin(7))
TiltServo.freq(50)
TiltServo.duty_u16(Tcentre)

################################################################################
# Main Loop

dataM = [0] * 6
LeftPower, RightPower = 0, 0

def GetData():
    global dataM
    dataM[0] = dataV[0]
    dataM[1] = dataV[1]

    GetMotorI()
    dataM[2] = LMamps
    dataM[3] = RMamps
    dataM[4] = LeftPower
    dataM[5] = RightPower

Scheduler = 0
LEDupdate('GreenSolid')
Mode = 'Normal'

while True:
    sleep_ms(1)
    Scheduler += 1

    if (Scheduler - 2) % 50 == 0: 
        # ch1-6 ===  dataR[0]-[5]
        if Mode == 'RC':
            if dataR[0] > 10:                       # as THR off defaults to about 7%               
                dd = int(dataR[0] / 100 * 2**16)    # ch1 thro: PWM
                if dataR[4] < 90:                   # ch5 gear: direction
                    MotDrive(dd,dd)
                else:
                    MotDrive(-dd,-dd)
            else:
                MotDrive(0, 0)
            
            S = (dataR[1]-50) / 50      #ch2 aile: steering
            if S > 0.02:
                y = Scentre + ((Shigh - Scentre) * S) 
            elif S < -0.02:
                y = Scentre + ((Scentre - Slow) * S) 
            else:
                y = Scentre
            SteeringServo.duty_u16(int(y))


            T = (dataR[2]-50) / 50      #ch3 elev: camera tilt
            if T > 0.05:
                y = Tcentre + ((Thigh - Tcentre) * T) 
            elif T < -0.05:
                y = Tcentre + ((Tcentre - Tlow) * T) 
            else:
                y = Tcentre
            TiltServo.duty_u16(int(y))


    if (Scheduler - 10) % 100 == 0:          #100ms 10ms offset
        if RecvCommand(Muart):
            print('New Command: ', dataCMD)

    if (Scheduler - 20) % 200 == 0:    
        GetData()                       
        SendTelemetry(Muart, dataM, dataR)      
        print(dataR, dataM)   

        if dataR[5] > 80:
            if Mode == 'Normal':
                Mode = 'RC'
                LEDupdate('PinkFlash')
        else:
            if Mode == 'RC':
                Mode = 'Normal'
                MotDrive()  
                SteeringServo.duty_u16(Scentre)
                TiltServo.duty_u16(Tcentre)
                LEDupdate('GreenSolid')

        collect()

    if (Scheduler - 33) % 250 == 0:  
        LEDupdate()                         # aka flash if selected

    if (Scheduler - 20) % 1000 == 0:         #1000ms 5ms offset   
        pass
        #collect()

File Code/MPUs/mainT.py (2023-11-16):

################################################################################
# Roverling Mk II - Telemetry Processor
print('Roverling Mk II - Telemetry Processor main.py on RP2040')

from machine import Pin, I2C, UART, ADC
from time import sleep_ms, sleep_us, ticks_ms, ticks_us
from gc import collect
import neopixel
from cryptolib import aes

# my modules
from GPS import ReadGPS, dataGPS
from IMU import ReadIMU, dataIMU
from Packets import AssemPkt_T, DisAssemPkt_T, AssemPkt_C, DisAssemPkt_C
from Comms import RecvTelemetry, dataMOT, SendCommand
import PIO_UART

Tuart = UART(1, baudrate=1_000_000, tx=Pin(4), rx=Pin(5))

################################################################################
# LED
NeoPin = Pin(16,Pin.OUT)
Neo = neopixel.NeoPixel(NeoPin,1)
LastLEDstate = True
RGBon, RGBoff = (20,0,0), (0,0,0)

Neo[0]=(20, 0, 0)
neopixel.NeoPixel.write(Neo)

def LEDupdate(mode='none'):
    global Neo, LastLEDstate, RGBon, RGBoff

    if mode == 'GreenSolid':
        RGBon, RGBoff = (20,0,0), (20,0,0)
    elif mode == 'RedSolid':
        RGBon, RGBoff = (0,40,0), (0,40,0)
    elif mode == 'YellowFlash':
        RGBon, RGBoff = (6,20,0), (0,0,0)
    elif mode == 'PinkFlash':
        RGBon, RGBoff = (5,50,10), (0,0,0)
    elif mode == 'BlueSolid':
        RGBon, RGBoff = (0,0,30), (0,0,30)
    if not LastLEDstate:
        Neo[0] = RGBon
        LastLEDstate = True
    else:
        Neo[0] = RGBoff
        LastLEDstate = False

    neopixel.NeoPixel.write(Neo)

LEDupdate('RedSolid')

################################################################################
# LoRa

from sx1262 import SX1262
sx = SX1262(spi_bus=1, clk=10, mosi=11, miso=12, cs=3, irq=6, rst=7, gpio=2)
# Time On Air : Telemetry 64 bits, 195ms, Control 16 bits, 82ms
# At BW=250kHz, SF=9, CR=1/5, Date Rate = 1,758bps
# for max power current limit must be changed for 60 - 140 and LDO enabled
#
sx.begin(freq=920, bw=250.0, sf=9, cr=5, syncWord=0x12,
         power=22, currentLimit=140.0, preambleLength=8,
         implicit=False, implicitLen=0xFF,
         crcOn=True, txIq=False, rxIq=False,
         tcxoVoltage=1.7, useRegulatorLDO=True, blocking=True)

NewCmd = False
NewCmdPkt = [0x00] * 16
SNR, RSSI = 0.0, 0.0

def cbLoRa(events):
    global NewCmd
    global NewCmdPkt
    global SNR
    global RSSI
    if events & SX1262.RX_DONE:
        msg, err = sx.recv()
        error = SX1262.STATUS[err]
        if err == 0:
            NewCmd = True
            NewCmdPkt = msg
            SNR = sx.getSNR()
            RSSI = sx.getRSSI()
        else:
            print('LoRa Rx Error: ', error)
    elif events & SX1262.TX_DONE:
        pass                        #TX done    
    else:
        print('LoRa unknown interrupt: ', events)


VBatList = [0] * 9

################################################################################
# Battery Voltage 5cell LiPo system (https://blog.ampow.com/lipo-voltage-chart/)

Vbat = ADC(Pin(29))
def GetVbat():
    global VbatList
    VbatCoeff = 1170                        # through testing
    V = Vbat.read_u16() / VbatCoeff /10     #  10 cells, nom 36V
    #print(V)
    if   V >= 4.20:   cap = 100
    elif V >= 4.15:   cap = 95
    elif V >= 4.11:   cap = 90
    elif V >= 4.08:   cap = 85
    elif V >= 4.02:   cap = 80
    elif V >= 3.98:   cap = 75
    elif V >= 3.95:   cap = 70
    elif V >= 3.91:   cap = 65
    elif V >= 3.87:   cap = 60
    elif V >= 3.85:   cap = 55
    elif V >= 3.84:   cap = 50
    elif V >= 3.82:   cap = 45
    elif V >= 3.80:   cap = 40
    elif V >= 3.79:   cap = 35
    elif V >= 3.77:   cap = 30
    elif V >= 3.75:   cap = 25
    elif V >= 3.73:   cap = 20
    elif V >= 3.71:   cap = 15
    elif V >= 3.69:   cap = 10
    elif V >= 3.61:   cap = 5
    else:             cap = 0

    # get median over 9 samples
    VBatList.append(cap)
    VBatList.pop(0 )
    tmpList = []
    tmpList.extend(VBatList)
    tmpList.sort()
    return(tmpList[4])

################################################################################
Vsonar = ADC(Pin(27))
def GetSonar():
    global Sonar
    VsonarCoeff = 9.0
    S = Vsonar.read_u16() / VsonarCoeff
    return int(S)

Vpir = Pin(28, Pin.IN, Pin.PULL_UP)
def GetPIR():
    if Vpir.value() == 1:
        return True
    else:
        return False

def set_bit(value, bit):
    return value | (1<<bit)

def clear_bit(value, bit):
    return value & ~(1<<bit)

dataOther = [0] * 6
def GetOtherData():
    global dataOther
    dataOther[0] = SNR
    dataOther[1] = RSSI
    dataOther[2] = GetSonar()
    dataOther[3] = GetVbat()
    
    PIR = GetPIR()
    # Next two bit wise operations only
    if PIR:
        dataOther[4] = set_bit(dataOther[4],0)
    else:
        dataOther[4] = clear_bit(dataOther[4],0)
    dataOther[5] = 0
    return

################################################################################
# Main 
LEDupdate('GreenSolid')

sx.setBlockingCallback(False, cbLoRa)
Scheduler = 0

while True:
    sleep_ms(1)
    Scheduler += 1

    if (Scheduler - 0) % 100 == 0:          #100ms 0ms offset
        ReadGPS()
        
        if NewCmd:
            LEDupdate('BlueSolid')
            NewCmd = False
            vals,ss = DisAssemPkt_C(NewCmdPkt)
            SendCommand(Tuart, ss)

            #PIO_UART.WriteLine('Commands' + ss + '\n')  

    if (Scheduler - 50) % 100 == 0:          #100ms 0ms offset
        LEDupdate('GreenSolid')

    if (Scheduler - 10) % 100 == 0:         #100ms 10ms offset          
        RecvTelemetry(Tuart)
        pass
            
    if (Scheduler - 20) % 1000 == 0:      
        ReadIMU()
        #print(dataIMU[6],dataIMU[7],dataIMU[8])


    if (Scheduler - 30) % 100 == 0:      
        collect()

    if (Scheduler - 40) % 500 == 0:  
        GetOtherData()
        #print(dataGPS, dataMOT, dataIMU, dataOther)
        x = AssemPkt_T(dataGPS, dataMOT, dataIMU, dataOther)
        try:
            sx.send(x)      
        except:
            print('Send failed')

        PIO_UART.WriteLine('GPS Time ' + str(dataGPS[0]) + '\n')

        #x = PIO_UART.ReadLine()
        #print(x)

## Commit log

2023-08-18 second try
    [R205-Antenna-Base-R1.3mf, R205-Antenna-Base.stl, R205-Antenna-Cover-R1.3mf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]
2023-10-24 Reorg 3D directory
    [R205-Antenna-Base-R1.3mf, R205-Antenna-Base.stl, R205-Antenna-Cover-R1.3mf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]
2023-10-24 updated 3D
    [R206-Servo-Horn-R3.3mf, R206-Servo-Horn.stl, R207-Antenna-Bracket-R1.3mf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]
2023-10-24 Electronics section now added. schematic diagram and wiring pics
    [R202.csv, R202.kicad_pcb, R202.kicad_sch]
2023-10-25 Adding in Raspberry Pi 4 code
2023-11-12 Error fix, power net to LoRa module moved from incorrect pin 39 to correct pin 36
    [R202.kicad_sch]
2023-11-16 New LoRa gateway 3D model added, Prusa, Gcode and STL mainT.py (telemetry processor), UART to RPi4 implemented. Only send/Tx works reliably PIO_UART.py. Still no success under Python in a production 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
    [LoRaGateWay101-Base-R1.3mf, LoRaGateWay101-Base.stl, LoRaGateWay101-Top-R1.3mf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]
